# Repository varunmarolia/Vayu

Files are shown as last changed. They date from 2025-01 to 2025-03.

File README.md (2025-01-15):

# Vayu
Vayu is a smart ventilation system with heat recovery

# Problem
During winter time when the temperature is in single digit or below, the windows are kept shut and sealed so that radiators can work their magic.
The quality of indoor air gets very bad as the day goes by. The current ventilation system is basically a hole (ranging rom 100mm to 150mm in diameter) in the wall with some filter and vent with open/close mechanism.
This system does not provide enough air flow inside room specifically when the room is sealed. In order to make the indoor quality better the air needs to be forced/pumped inside the room.
Since the outside temperature is very low it needs to be heated and filtered before it can be pulled inside the room. 

# Focus of the project
- The aim of the project is to provide a ventilation system that can provide fresh room temperature air. We do this by recovering the heat from the air in the room itself.
- The system must be smart enough such that the "Heat recovery" should be performed automatically. i.e. if the outside temperature air is cold, turn on the heat recovery, if not just do normal ventilation.
- The design must be a quiet one, so we can sleep peacefully.
- Proper condensation management and defrosting functions.
- The system should have wireless capabilities in order to be an IoT device in the future.

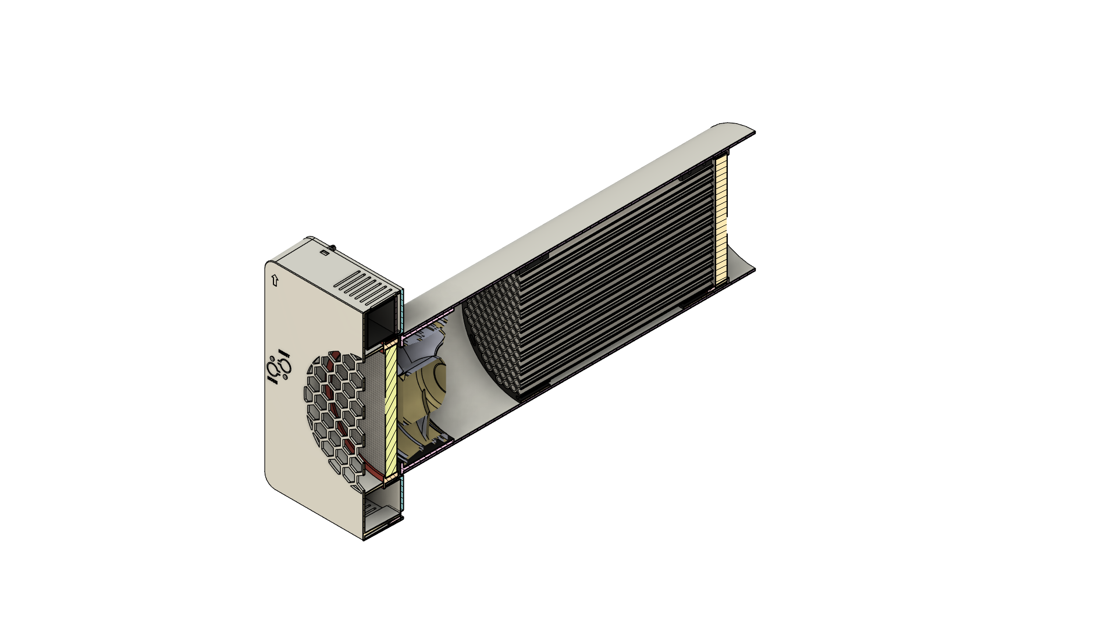
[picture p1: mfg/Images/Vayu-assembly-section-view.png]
Vayu full assembly Vayu-assembly-section-view-image

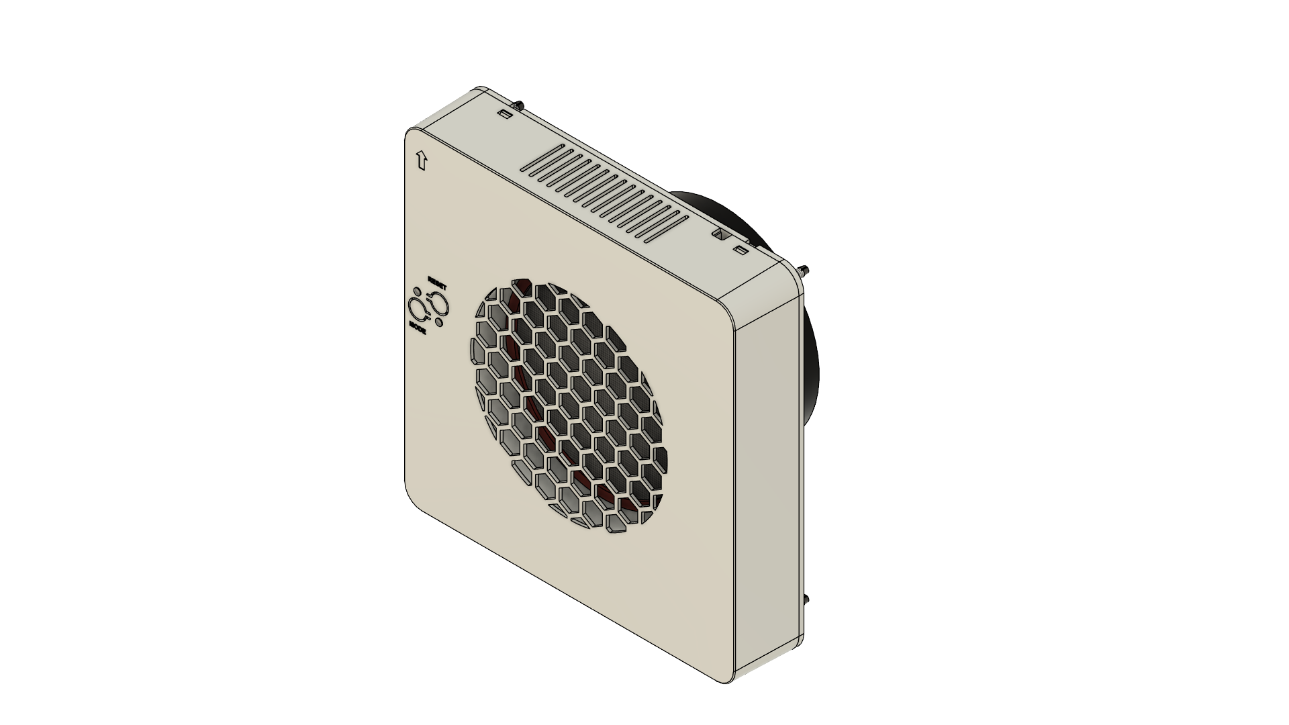
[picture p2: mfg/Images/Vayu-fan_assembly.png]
Vayu fan assembly Vayu-fan_assembly-image

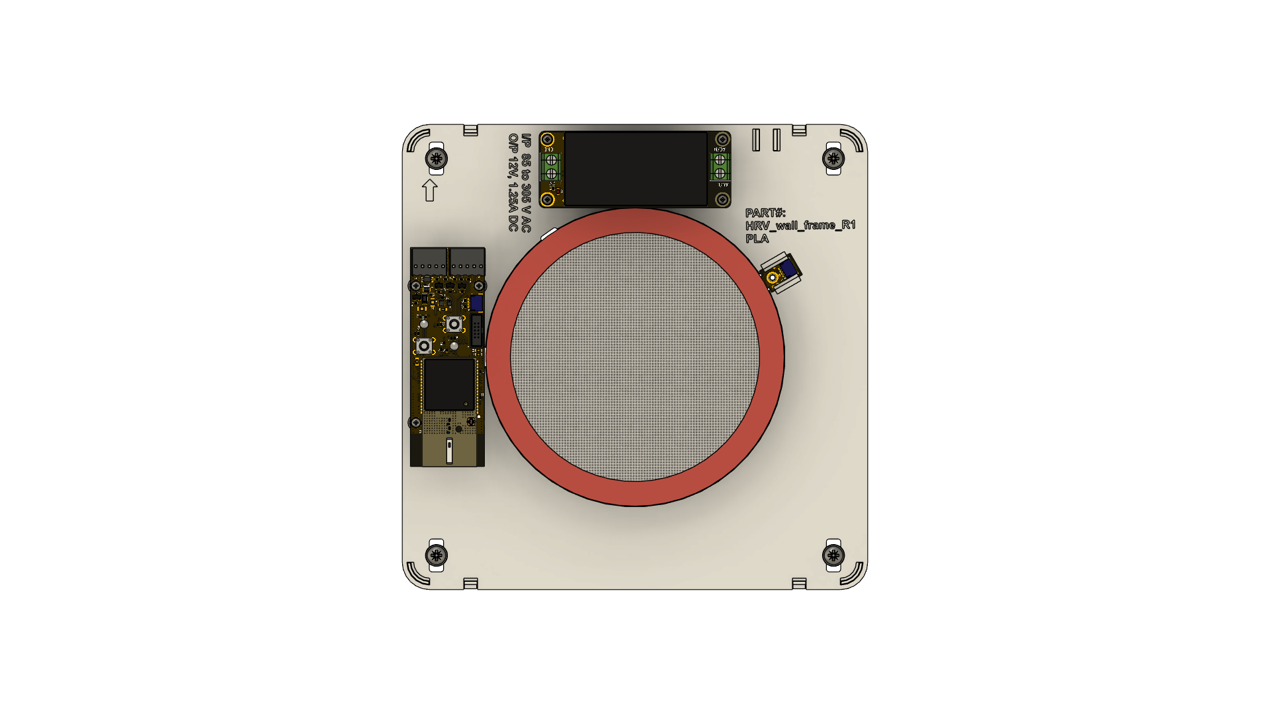
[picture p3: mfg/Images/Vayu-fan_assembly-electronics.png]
Vayu el assembly Vayu-el-image

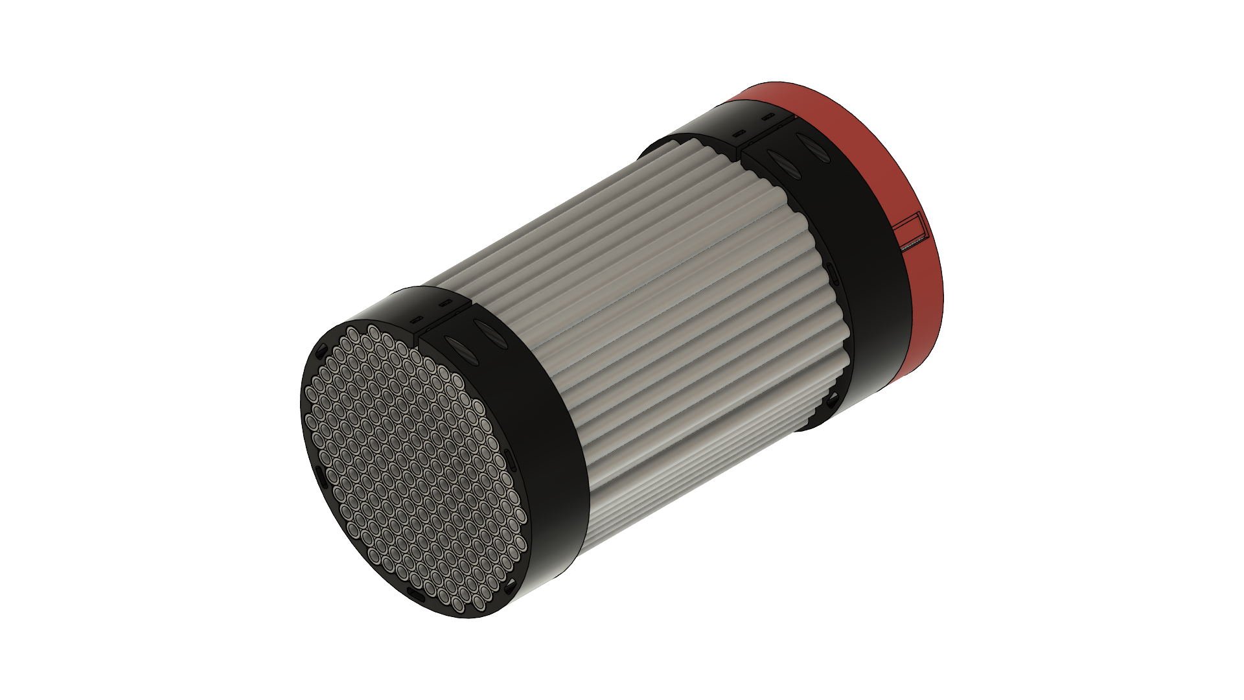
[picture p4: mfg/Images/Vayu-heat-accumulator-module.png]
Vayu heat accumulator Vayu-heat-accumulator-image


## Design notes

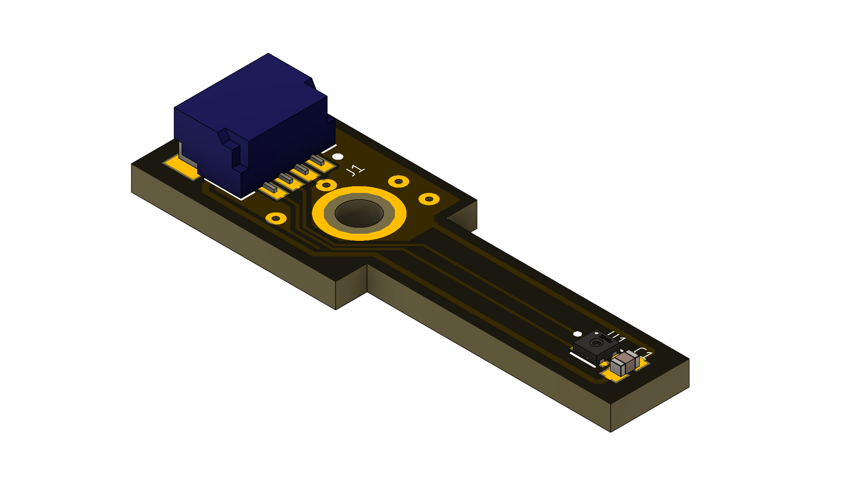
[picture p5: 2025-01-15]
mfg/Images/vayu_i2c-R1A-pcb-top-side.png

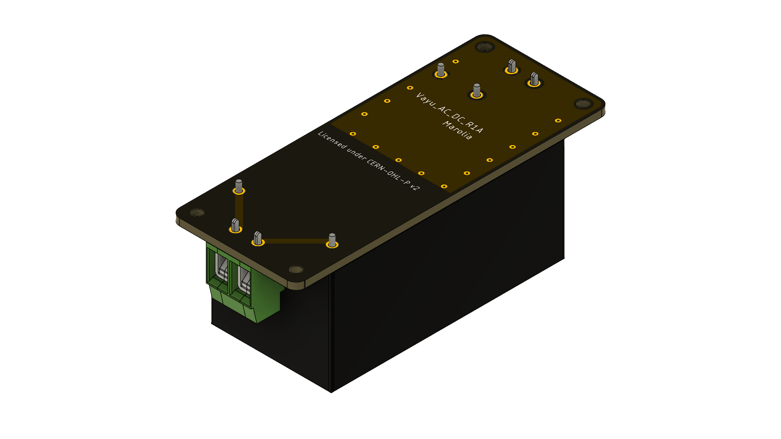
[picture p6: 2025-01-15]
mfg/Images/Vayu_AC_DC-R1A-pcb-bottom-side.png

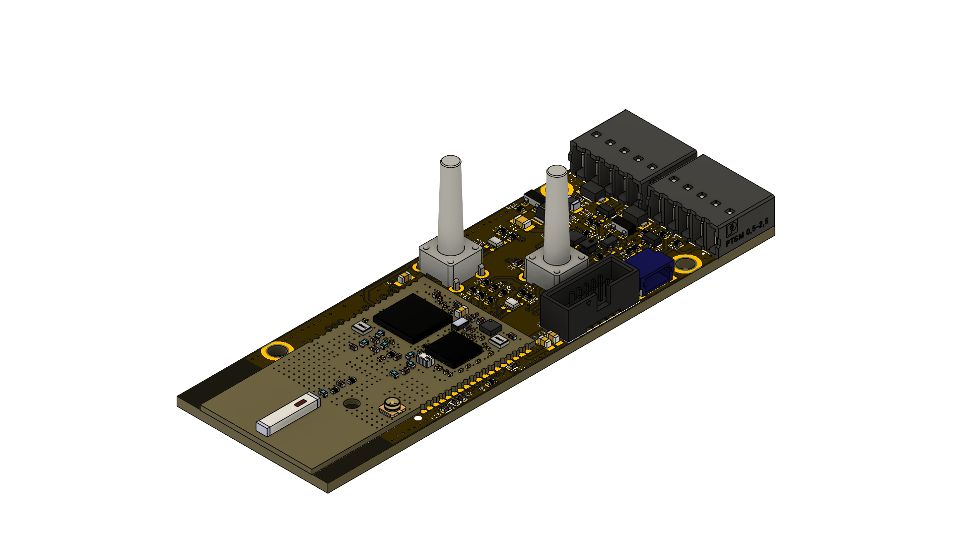
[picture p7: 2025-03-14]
mfg/Images/vayu-R1A-pcb_top_side.png

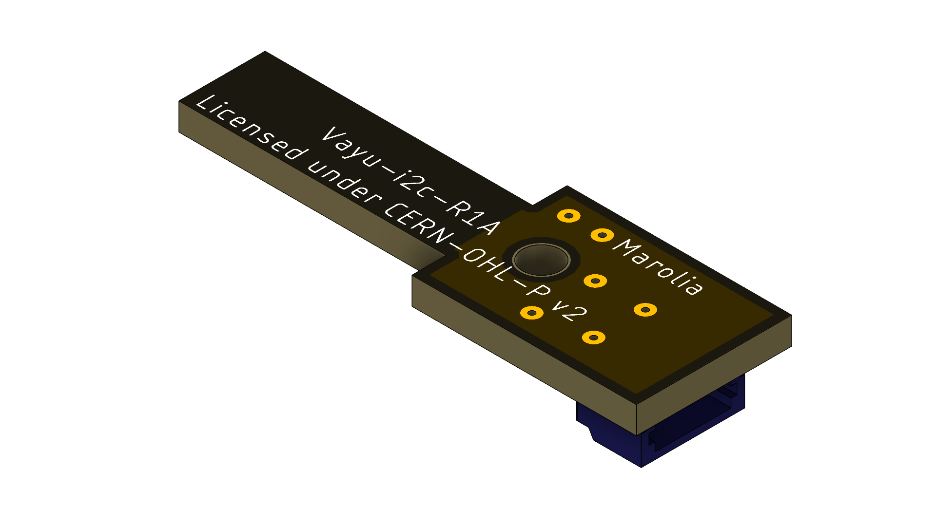
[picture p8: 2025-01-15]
mfg/Images/Vayu_i2c-R1A-pcb-bottom-side.png

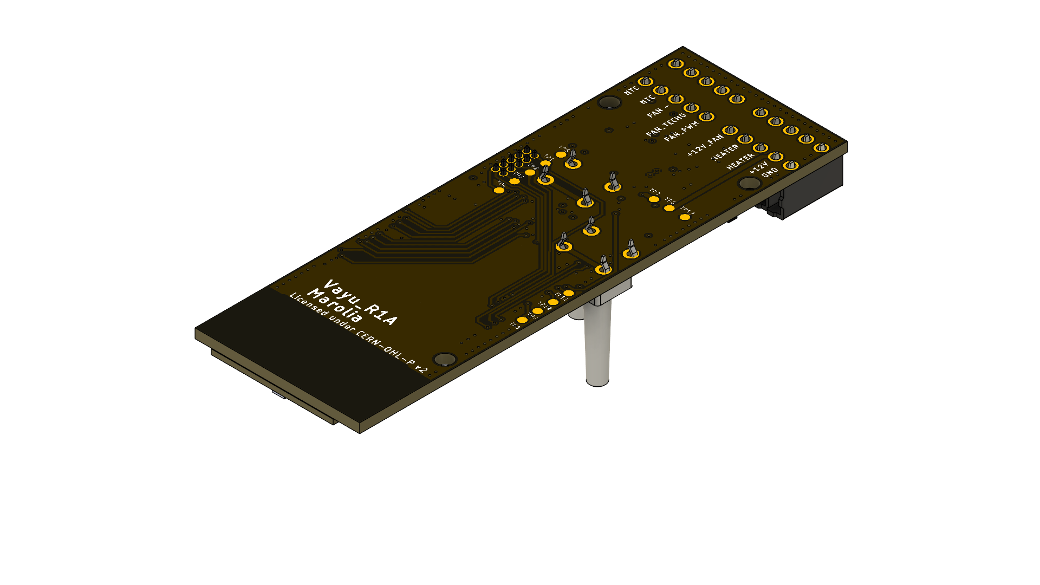
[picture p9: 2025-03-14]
mfg/Images/Vayu-R1A-pcb-bottom-side.png

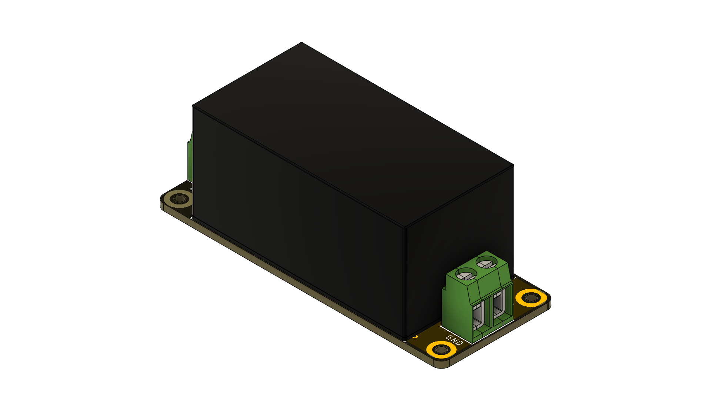
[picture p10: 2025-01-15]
mfg/Images/Vayu_AC_DC-R1A-pcb-top-side.png

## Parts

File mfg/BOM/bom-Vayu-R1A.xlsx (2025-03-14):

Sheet: Information
Title: | BILL OF MATERIAL
Project: | Vayu
Document: | bom-Vayu-R1A
Revision: | A
Date: | Oct/01/2024
PCBA P/N: | PCBA-Vayu-R1A
Notes:
Tab "No Mount" contains items that is not to be mounted
The revision of the BOM is same as revision of the Schematic
There are three different catagories of components
Cat "A" means component does not have any alternate manufacturers available
Cat "B" must choose from the list of manufacutrers provided
Cat "C" Can choose any manufacutrer as long as specifications for the components are met
PCBA part number is made of "PCBA-<code_name>-<pcb rev><schematic rev>
Changes in rev A |  | Oct/01/2024
Component | Part Reference | Comment
- | - | -

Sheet: Vayu
Marolia - Compressed sheet - Project: Vayu, Doc: bom-Vayu-R1A, Rev: A, Date: Oct/01/2024
Value | Title | Package | Qty | References | Assy | Cat | Mfr | Mfr PN | Mfr2 | Mfr PN2 | Mfr3 | Mfr PN3
1M | RESISTOR, 1%, 1/16W, SMT, RoHS | R0402 | 1 | R2 | SMT | C | Yageo | RC0402FR-071ML | Samsung | RC1005F105CS
10K | RESISTOR, 1%, 1/16W, SMT, RoHS | R0402 | 7 | R5, R3, R15, R16, R17, R23, R26 | SMT | C | Yageo | RC0402FR-0710KL | Samsung | RC1005F103CS
220E | RESISTOR, 1%, 1/16W, SMT, RoHS | R0402 | 4 | R18, R19, R20, R21 | SMT | C | Yageo | RC0402FR-07220RL | Samsung | RC1005F221CS
200K | RESISTOR, 1%, 1/16W, SMT, RoHS | R0402 | 2 | R22, R10 | SMT | C | Yageo | RC0402FR-07200KL
47K | RESISTOR, 1%, 1/16W, SMT, RoHS | R0402 | 2 | R7, R24 | SMT | C | Yageo | RC0402FR-1347KL | Bourns Inc. | CR0402-FX-4702GLF
100K | RESISTOR, 1%, 1/16W, SMT, RoHS | R0402 | 9 | R1, R4, R6, R8, R11, R12, R13, R14, R25 | SMT | C | Yageo | RC0402FR-07100KL | Samsung | RC1005F104CS
NCP15WF104F03RC | Thermistor, NTC, 100k OHM @ 25C, 1%, B=4250, 100mW, 0402 (1.0 x 0.5 x 0.5 mm), SMT, RoHS | R0402 | 1 | R9 | SMT | B | Murata | NCP15WF104F03RC
10uF | CAPACITOR, X5R, 6.3V, 20%, SMT, RoHS | C0603 | 3 | C1, C3, C4 | SMT | C | Murata | GRM188R60J106ME47D | Samsung | CL10A106MQ8NNNC
1nF | CAPACITOR, C0G NP0, 50V, 1%, SMT, RoHS | C0402 | 4 | C2, C12, C13, C14 | SMT | C | Murata | GCM1555C1H102FA16D | Yageo | AC0402FRNPO9BN102
10uF- 16V | CAPACITOR, X5R, 25V, 20%, SMT, RoHS | C0805 | 2 | C5, C11 | SMT | C | Murata | GRM21BR61E106MA73L | Samsung | CL21A106KACLRNC
22uF- 6V | CAPACITOR, X5R, 6.3V, 20%, SMT, RoHS | C0603 | 1 | C6 | SMT | C | Murata | GRM188R60J226MEA0D | Samsung | CL10A226MP8NUNE
0.1uF | CAPACITOR, X7R, 16V, 10%, SMT, RoHS | CAPC1005X55N | 4 | C7, C8, C9, C10 | SMT | C | Murata | GRM155R71E104KE14J | Samsung | CL05B104KO5NNNC
SMF12CA | Diode, Reverse standoff 12Volt- Breakdown 13.3V- 19.9V Clamp 10.1A Ipp Tvs Diode Surface Mount SOD-123F | SOD-123F-BI | 2 | D1, D3 | SMT | B | Littelfuse Inc. | SMF12CA | Shenzhen Slkormicro Semicon Co., Ltd. | SMF12CA
B240S1F-7 | Diode, MBR1020VL Surface Mount Schottky Power rectifier, >1.5Amp, DC reverse Max 16V | SOD-123F | 1 | D2 | SMT | B | Diodes Incorporated | B240S1F-7 | Diodes Incorporated | MBR230S1F-7
BLM21PG600SH1D | Ferrite bead, 60 Ohms @ 100 MHz 1 Power Line Ferrite Bead 0805 (2012 Metric) 3.5A 20mOhm | BEADC2012X105N | 1 | FB1 | SMT | B | Murata | BLM21PG600SH1D | Bourns Inc. | MH2029-600Y
CON-1770911 | Connector, 5 Position Wire to Board Terminal Block Horizontal with Board 0.098 (2.50mm) Through Hole | PHOENIX_1770911 | 2 | J1, J2 | TH | A | Phoenix Contact | 1770911
3220-10-0100-00 | Connector, Header Through Hole 10 position 0.050 (1.27mm) | PIN2X5_1.27MM | 1 | J3 | SMT | A | CNC Tech | 3220-10-0100-00
SM04B-SRSS-TB(LF)(SN) | Connector, Header Surface Mount, Right Angle 4 position 0.039" (1.00mm) | JST_SM04B-SRSS-TB(LF)(SN) | 1 | J4 | SMT | A | JST Sales America Inc. | SM04B-SRSS-TB
2.2uH- 1.84A | indcutor, 2.2 uH Shielded Drum Core- Wirewound Inductor 1.85 A 137mOhm Max 0806 (2016 Metric) | IND_VLS201612HBX-2R2M-1 | 1 | L1 | SMT | B | TDK Corporation | VLS201612HBX-2R2M-1 | Taiyo Yuden | MEKK2016H2R2M
IRLML6402TRPBF | MOSFET, P-Channel 20V 3.7A (Ta) 1.3W (Ta) Surface Mount SOT-23 | SOT23-3 | 2 | Q2,Q4 | SMT | C | Infineon | IRLML2244TRPBF | Taiwan Semiconductor Corporation | TSM650P02CX RFG
BSS138PW | MOSFET, N-Channel 60 V, 320 mA N-channel Trench MOSFET | SC-70 | 1 | Q1 | SMT | B | Nexperia USA Inc. | BSS138PW,115
DMN2056U-7 | N-Channel 20 V 4A (Ta) 940mW Surface Mount SOT-23-3 | SOT23-3 | 1 | Q3 | SMT | B | Diodes Incorporated | DMN2056U-7
MMBT4401WT1G | Bipolar (BJT) Transistor NPN 40 V 600 mA 250MHz 150 mW Surface Mount SC-70-3 (SOT323) | SC-70 | 1 | Q5 | SMT | B | Onsemi | MMBT4401WT1G
TL1105LF160Q | SWITCH, TACTILE SPST-NO 0.05A 12V 6x6mm. Actuator height from PCB 17mm | TACT_TH_6X6X17MM | 2 | SW1, SW2 | SMT | C | E-Switch | TL1105LF160Q
efr32-cc1200-rf | RF Module, Akshavani1 2.4GHz- 868/915 MHz radio module | AKASHVANI1 | 1 | U1 | SMT | A | Self | Akashvani1
TPS62172DSGT | Voltage regulator, TPS6217x 3-V to 17-V- 0.5-A Step-Down Converter swith DCS-Control | SON50P200X200X80-9N | 1 | U2 | SMT | A | Texas Instruments | TPS62172DSGT
APTB1615YSGC-F01 | LED, Bi-color, 568nm green/627nm red, 2.2V, 20mA, 1.6 x 1.5 mm, 0.7mm H, 4 pin, SMT, RoHS | LED-0606 | 2 | V1, V2 | SMT | B | Kingbright | APTB1615YSGC-F01

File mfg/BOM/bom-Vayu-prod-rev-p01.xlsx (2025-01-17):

Marolia - Top Level BOM for Vayu-R1A, Date: 2024-12-12, Rev: P01
Value | Title | Qty | Mfr | Mfr PN | Note
LFB075CTP | Light Pipe, 3mm dia, 19mm length, Single Clear, Diffused Rigid Panel Mount, Press Fit, Front | 2 | VCC | LFB050CTP | Front face center LED light pipe
1052620001 | Antenna, 866MHz, 915MHz Flat Patch, 0.4dBi, 1.4dBi U.FL (UMCC), IPEX MHF1 Adhesive | 1 | Molex | 1052620001 | Optinal Sub-GHz antenna
product-label | Fasson Transfer PET 75 / S8015 Matt silver heavy duty label 40mm x 25 mm | 1 | Fasson | PET75/S8015 | Silver label applied on back of the bottom plastic case
Vayu-front_shell | Mec, Front shell | 1 | 3d print | Vayu-front_shell
Vayu-wall_mounting_frame | Mec, Vayu wall mounting frame | 1 | 3d print | Vayu_wall_frame
Vayu-fan-shroude | Mec, Vayu fan shroude | 1 | 3d print | Vayu_fan_shroude
Vayu-filter_cap_front | Mec, Vayu filter cap front | 1 | 3d print | Vayu_filter_cap_front
heat_accumulator_filter_cap_back | Mec, heat-accumulator filter cap back | 1 | 3d print | Vayu_filter_cap_back
heat_accumulator_shroud | Mec, heat-accumulator shroud | 2 | 3d print | Vayu_heat_accumulator_shroude
Vayu-filter | Filter pad, 96 mm diameter | 2 | Flexit | friskluftsventil 100FF | Custom cut to 96mm diameter
PVC-pipe | Pipe, 100m diameter. 300mm length | 1 | Flexit | Flexit RG100 | Custom cut to wall length
M4 screw fan | screw,M4 x 16mm, self tapping plastic screw | 2 | Amazon
Anchor | Super plug, NY, 5mm hole, 25mm length, EXPANDET | 4 | Amazon
M4 wall screw | screw, M4 x 16mm length | 4 | Amazon
M2 screw | screw, M2.0, 5mm Length, Pan head, Philips OR Rouded head Torx Thread-forming screw for plastic | 8 | Amazon
M2 Nut | Nut, M2, Hex nut, 1.5mm thick, 3.8mm length | 4 | Amazon
SanAce_9RF_92x38_RBD | Fan Tubeaxial 12VDC Round - 92mm Dia Ball 42.4 CFM (1.19m³/min) 4 Wire Leads | 1 | Sanyo Denki America Inc. | 9RF0912P1H001
Vayu-R1A-PCBA | PCBA, Vayu-R1A, Assembled | 1 | Self assembled | Vayu-R1A-PCBA
Vayu_i2c-PCBA | PCBA, Vayu-i2c-R1A, Assembled | 1 | Self assembled | Vayu-i2c_R1A-PCBA
Vayu_AC_DC-PCBA | PCBA, Vayu_AC_DC-R1A, Assembled | 1 | Self assembled | Vayu_AC_DC-R1A-PCBA
Aluminium tubes | Tube, Aluminim, ID4mm, OD6mm, 166mm length | 211 | Kaiserthal | N/A | Bought from Hornbach and custom cut to 166mm
JST cable connector | 4 Position Cable Assembly Rectangular Socket to Socket, Reversed 0.667' (203.20mm, 8.00") | 1 | JST Sales America Inc. | A04SR04SR30K203A
AC-plug | plug, 2 pin AC cord, EU type, 2.5 meter | 1 | Amazon
magnet | magnet, Neodeam, 20mm x 10mm x 2mm | 1 | Amazon
Aluminium tape | tape, 50mm width, 250mm length, Metallic searing tape for high and low temperature channels, waterproof | 1 | Tesa | Tesa-60672
NTC-100K-probe | probe, NTC temperature probe, 100K, B3950 Thermistor, OD3mm Cartridge sensor | 1 | Amazon |  | Used in 3d printer extruder hot ends
Polymide-film-heater | Heater, Polymide film, 12Volt, 10watts, 30mm x 90mm | 1 | Amazon
Revision History
Rev | Date | Changes
P01 | 2024-12-12 | Initial release

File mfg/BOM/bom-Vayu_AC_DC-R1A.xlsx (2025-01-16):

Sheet: Information
Title: | BILL OF MATERIAL
Project: | Vayu_AC_DC
Document: | bom-Vayu_AC_DC-R1A
Revision: | A
Date: | DEC/01/2024
PCBA P/N: | PCBA-Vayu-R1A
Notes:
Tab "No Mount" contains items that is not to be mounted
The revision of the BOM is same as revision of the Schematic
There are three different catagories of components
Cat "A" means component does not have any alternate manufacturers available
Cat "B" must choose from the list of manufacutrers provided
Cat "C" Can choose any manufacutrer as long as specifications for the components are met
PCBA part number is made of "PCBA-<code_name>-<pcb rev><schematic rev>
Changes in rev A |  | Dec/01/2024
Component | Part Reference | Comment
- | - | -

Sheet: bom-Vayu_AC_DC-R1A
Marolia - Compressed sheet - Project: Vayu_AC_DC, Doc: bom-Vayu_AC_DC-R1A, Rev: A, Date: DEC/01/2024
Value | Description | Package | Qty | Reference | Assy | Cat | Mfr | Mfr PN | Mfr2 | Mfr PN2 | Mfr3 | Mfr PN3
CON-691137710002 | WR-TBL Serie 1377 - 5.00 mm Horiz Entry w. Pressure Clamp Glow Wire | TH-5MM | 2 | J1, J2 | TH | C | Würth Elektronik | 691137710002 | Same Sky (Formerly CUI Devices) | TB003-500-P02BE | Adam Tech | EBBA-02-C-SS-BU
IRM-15-12 | Meanwell Enclosed AC DC Converters 1 Output 12V 1.25A 85 ~ 305 VAC- 120 ~ 430 VDC Input | IRM-15 Series | IRM-15-12 | 15 watts | 12 volts | CONV_IRM-15-12 | 1 | PS1 | TH | A | Meanwell | IRM-15-12
680R | RESISTOR, 1%, 1/16W | R0402 | 1 | R1 | SMT | C | Yageo | RC0402FR-07680RL | Bourns Ic. | CR0402-FX-6800GLF
LED_RED | LED, Red 624nm LED Indication - Discrete 2V 0603 (1608 Metric) | CHIP-LED0603 | 1 | V1 | SMT | C | Harvatek Corporation | B1911USD-20D000114U1930 | Rohm Semiconductor | SML-D12U1WT86

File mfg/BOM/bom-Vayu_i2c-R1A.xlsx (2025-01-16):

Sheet: Information
Title: | BILL OF MATERIAL
Project: | Vayu
Document: | bom-Vayu_i2c-R1A
Revision: | A
Date: | Oct/01/2024
PCBA P/N: | PCBA-Vayu_i2c-R1A
Notes:
Tab "No Mount" contains items that is not to be mounted
The revision of the BOM is same as revision of the Schematic
There are three different catagories of components
Cat "A" means component does not have any alternate manufacturers available
Cat "B" must choose from the list of manufacutrers provided
Cat "C" Can choose any manufacutrer as long as specifications for the components are met
PCBA part number is made of "PCBA-<code_name>-<pcb rev><schematic rev>
Changes in rev A |  | Oct/01/2024
Component | Part Reference | Comment
- | - | -

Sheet: bom-Vayu_i2c-R1A
Marolia - Compressed sheet - Project: Vayu, Doc: bom-Vayu_i2c-R1A, Rev: A, Date: Oct/01/2024
Value | Title | Package | Qty | Reference | Assy | Cat | Mfr | Mfr PN | Mfr2 | Mfr PN2 | Mfr3 | Mfr PN3
0.1uF | CAPACITOR, X7R, 16V, 10%, SMT, RoHS | C0402 | 1 | C1 | SMT | C | Murata | GRM155R71E104KE14J | Samsung | CL05B104KO5NNNC
SHT40-AD1F-R2 | IC, Humidity, Temperature 0 ~ 100% RH I2C ±1.8% RH 4 s Surface Mount | 4-WDFN Exposed Pad | 1 | U1 |  | A | Sensirion AG | SHT40-AD1F-R2
SM04B-SRSS-TB(LF)(SN) | Connector, Connector Header Surface Mount, Right Angle 4 position 0.039" (1.00mm) | JST_SM04B-SRSS-TB(LF)(SN) | 1 | J1 | SMT | A | JST Sales America Inc. | SM04B-SRSS-TB

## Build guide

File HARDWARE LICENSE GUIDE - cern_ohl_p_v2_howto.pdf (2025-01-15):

# Guide to the CERN-OHL-P v2

This document contains guidelines on how to apply the CERN-OHL-P v2 to a given hardware design, and on the use of hardware designs licensed under the CERN-OHL-P v2.

How to apply the CERN-OHL-P v2 to a hardware design Pre-requisite:

Authorship/ownership of the design must be clear and undisputed. Only the legal owner of the rights in the hardware design may decide under what conditions to make it available. If ownership is vested in more than one person/entity, there must be an agreement among the owners (or a chain of compatible licences from each of them) to release the hardware design as open hardware, and under the CERN-OHL-P v2 in particular.

The hardware design Source package

Pack all your hardware design Source files (e.g. for a Printed Circuit Board schematics, layout, documentation...) as well as the documents listed below in an archive file. This will ensure the licensee downloads everything in one go. It is best to archive the files using a format everybody can open. Schematics and layouts should be included in both source form and, should the design tool be proprietary, a format readable by everybody, such as pdf.

The following documents must be distributed together with the hardware design sources:

- Document containing the CERN-OHL-P v2
- This Guide
- A text file (plain ASCII file), where information can be added to but not removed from, noting that the design has been changed, and providing a date and information about the changes made by Licensee (see section 3.3.b of CERN-OHL-P v2) (e.g. CHANGES.TXT). A detailed list of changes would be helpful, as would a diff, but a description of the changes (e.g. “AC/DC power converter circuit removed as AC input no longer necessary”) is fine.

What to do with the hardware design Sources

Include in the hardware design Sources, for instance as a header, the following elements:
- a copyright notice reflecting actual ownership;
- a notice that the hardware design source is licensed under the CERN-OHL-P v2, possibly with a link to https://cern.ch/cern-ohl:

o “Licensed under CERN-OHL-P v2 or later”

o “Licensed under CERN-OHL-P v2”;

- a disclaimer of warranties;
- a source location, where others can find your design, if you wish to specify one;

The following is an example of header if CERN is the Licensor:

Copyright CERN 2020.

This source describes Open Hardware and is licensed under the CERN-OHL-P v2

You may redistribute and modify this documentation and make products using it under the terms of the CERN-OHL-P v2 (https:/cern.ch/cern-ohl). This documentation is distributed WITHOUT ANY EXPRESS OR IMPLIED WARRANTY, INCLUDING OF MERCHANTABILITY, SATISFACTORY QUALITY AND FITNESS FOR A PARTICULAR PURPOSE. Please see the CERN-OHL-P v2 for applicable conditions

Include in a part of the Source corresponding to a visible part of the Product (e.g. silkscreen or top copper for a Printed Circuit Board):

- the licence notice: “Licensed under CERN-OHL-P v2”

o Do not include the CERN logo or the copyright notice

- the source location if you wish it to appear on the Product, its packaging or documentation

How to deal with hardware designs licensed under the CERN-OHL-P v2
Generally speaking, you must always comply with any obligations applying to a particular design (detailed in a contract or accompanying licence). If you receive hardware designs licensed under the CERN-OHL-P v2, the obligations are to:
- Keep intact all the copyright and trademark notices that are on the hardware design Sources;
- Keep intact the references to the CERN-OHL-P v2;
- Keep intact the disclaimer of warranties.

If you modify hardware design that you received from someone else that is licensed under the CERN-OHL-P v2, you must

- Keep intact all the notices referred to above (although you may remove notices that are no longer relevant to your design (for example, if the design you are using contains a power supply and a processor board, and you are only using the processor board in your own design, you can remove the notices relating to the power supply, so long as you are sure they only relate to the power supply);
- Include notices that you have modified the hardware designs, giving a date and information about the modifications you have made (e.g. in a CHANGES.TXT file);
- Add the appropriate copyright notice to the modifications that were made;

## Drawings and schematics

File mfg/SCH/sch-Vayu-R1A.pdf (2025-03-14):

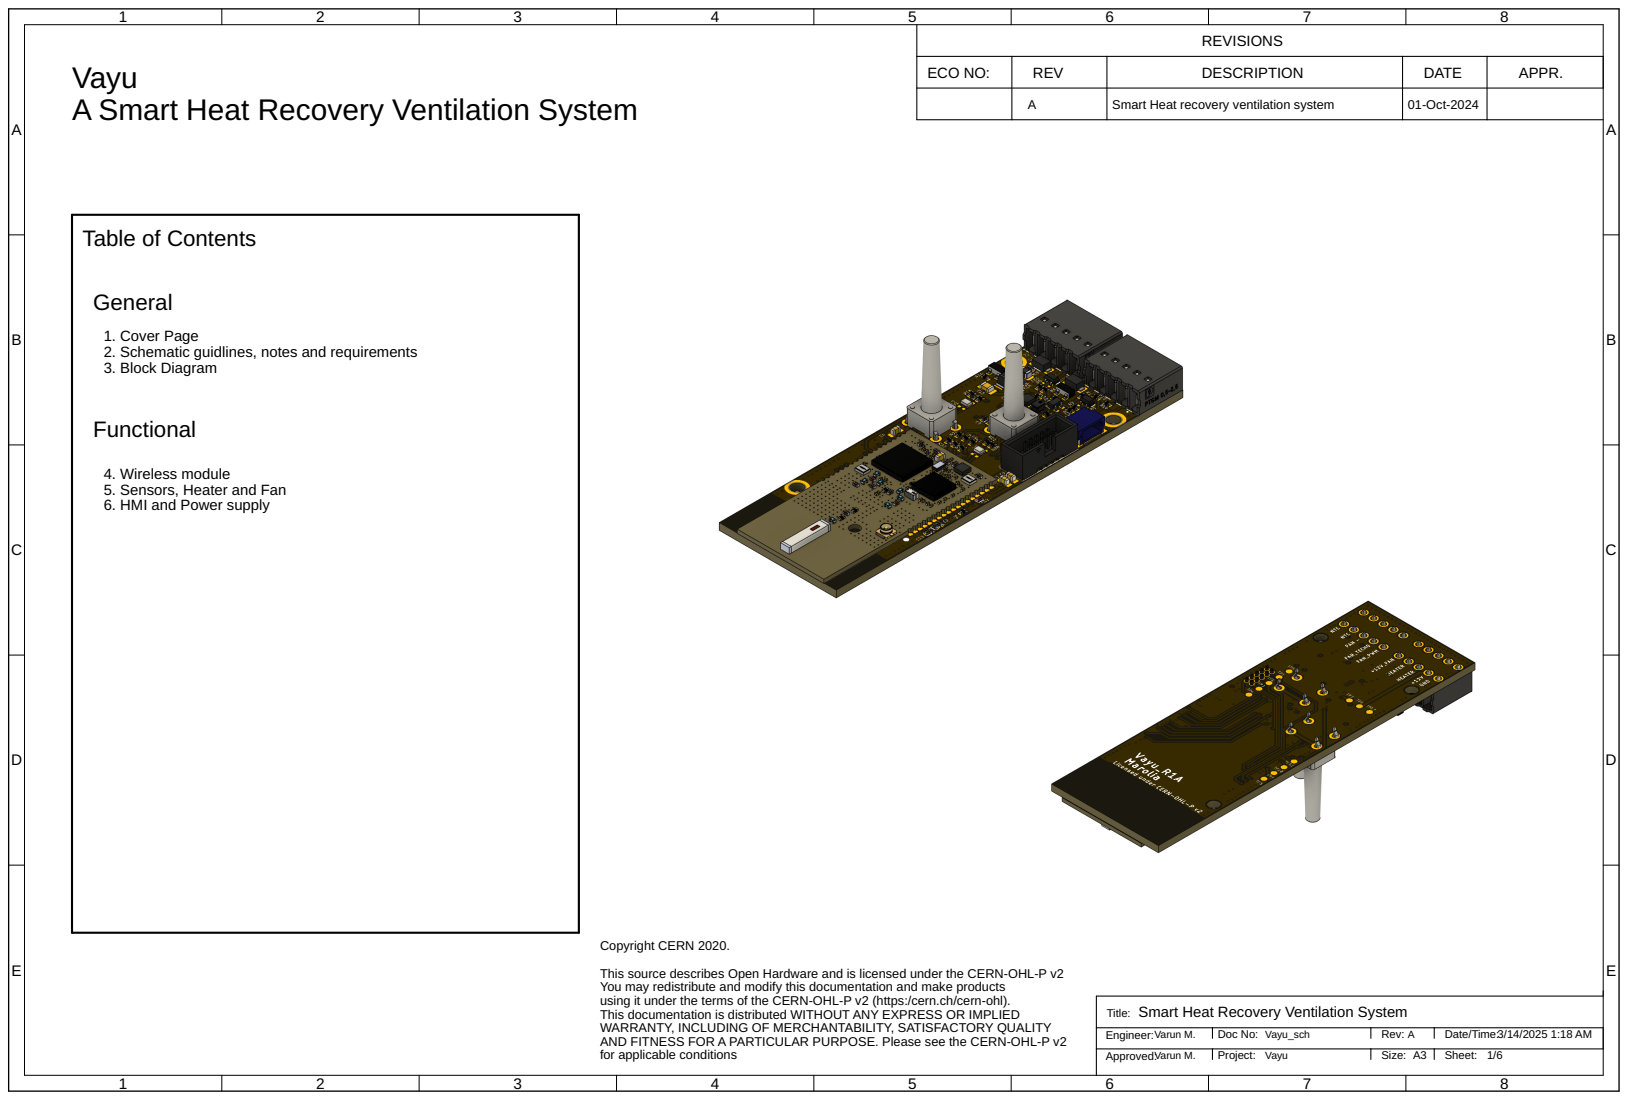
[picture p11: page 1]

REVISIONS

Vayu
A Smart Heat Recovery Ventilation System

ECO NO: | REV | DESCRIPTION | DATE | APPR.

A | Smart Heat recovery ventilation system | 01-Oct-2024

1. Cover Page
2. Schematic guidlines, notes and requirements
3. Block Diagram

4. Wireless module
5. Sensors, Heater and Fan
6. HMI and Power supply

Copyright CERN 2020. This source describes Open Hardware and is licensed under the CERN-OHL-P v2

You may redistribute and modify this documentation and make products
using it under the terms of the CERN-OHL-P v2 (https:/cern.ch/cern-ohl). This documentation is distributed WITHOUT ANY EXPRESS OR IMPLIED

Smart Heat Recovery Ventilation System

WARRANTY, INCLUDING OF MERCHANTABILITY, SATISFACTORY QUALITY
AND FITNESS FOR A PARTICULAR PURPOSE. Please see the CERN-OHL-P v2
for applicable conditions

Schematic guidelines, notes and requirements

# Schematic guidelines, notes and requirements

## Component guidelines

0 ohm resistors are 0402, 1A, unless otherwise noted. Capacitors are 0402, 10%, 50V unless otherwise noted. 0.047uF capacitors are 0402, 10%, 25V unless otherwise noted. 0.1uF, 0.22uF, 0.47uF and 1uF capacitors are 0402, 10%, 16V unless otherwise noted. 4.7uF, 10uF, and 22uF bulk capacitors are 0603, 6.3V/10V unless otherwise noted. Test point diameter is 1.2mm unless otherwise noted. Schematic guidelines

## General

IC pins that are internally pulled up or pulled down are indicated with the text PU or PD. All power nets normally starts with capital VDD* or VCC*. These nets should have planes by default. Graphic symbol description

Digital ground

Voltage connection

Test point (default size)

## Rules

Test points must be placed on the Secondary (bottom) side with a minimum 2.54mm spacing unless otherwise noted. Surface mount components on secondary side if any must be at least 4mm from thru hole pins. Not applicable for test

pins and debug headers (manually assembled when needed). Keep ground plane(s) away from the radio section of the wireless module. The 868/915 MHz radio on the wireless module uses external antenna that

must be encapulated inside the product case while avoiding proximity to any ground planes.

Sheet: Date/Time: Title: Engineer: | Doc No: | Rev: Approved: | Project: | Size: A3

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

A

B | B
C | C
D | D

E

A

E

3/14/2025 1:18 AM

2/6

Varun M. | Vayu_sch Vayu | A

Varun M.

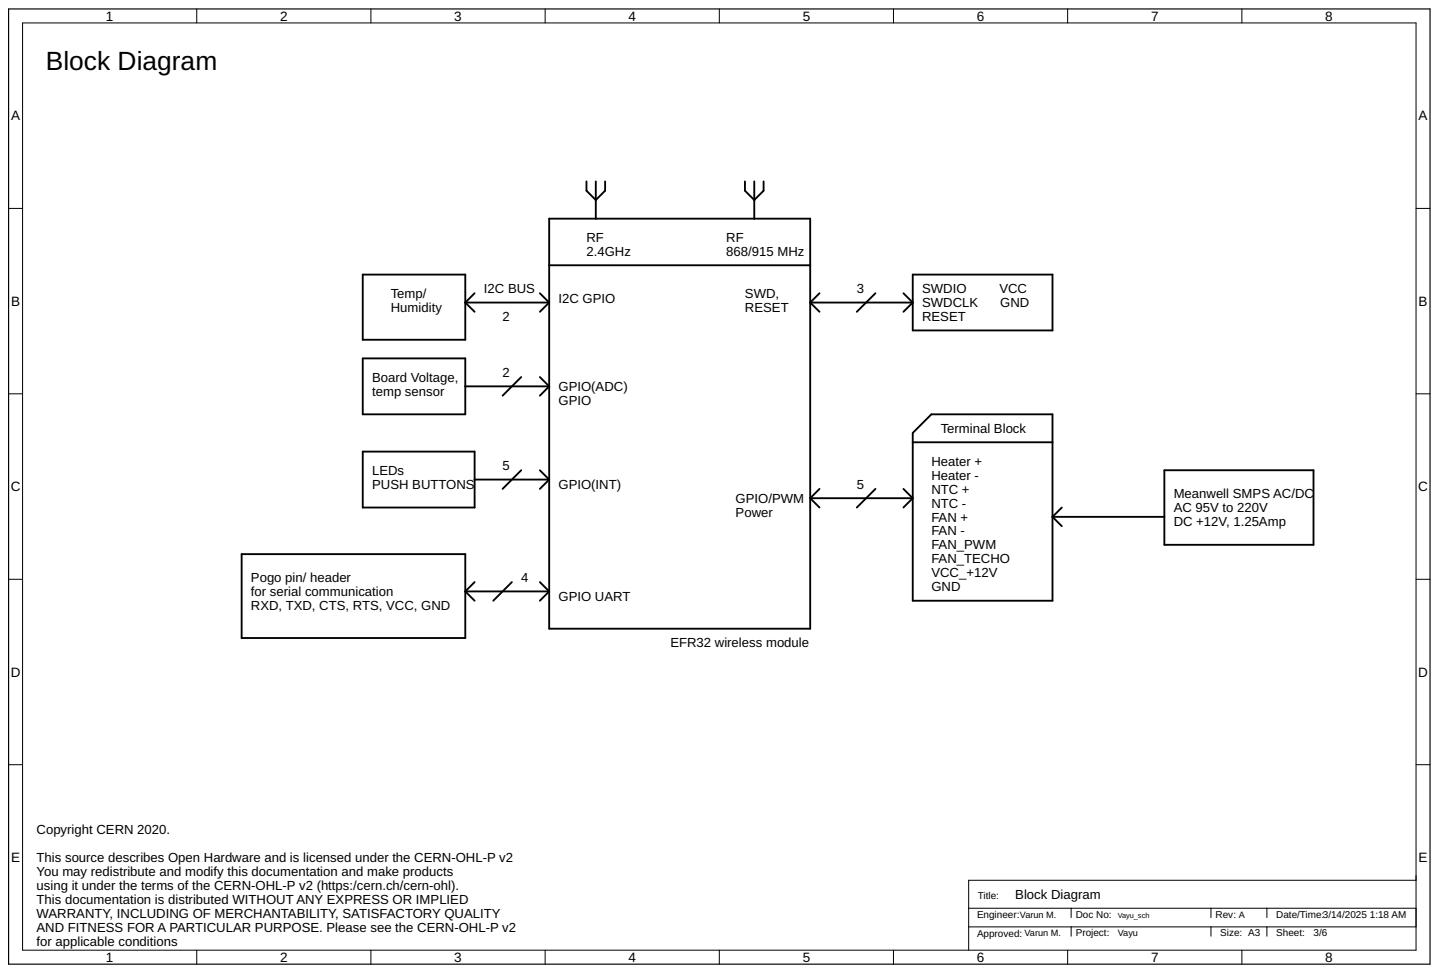
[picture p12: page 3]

Meanwell SMPS AC/DC
DC +12V, 1.25Amp

Pogo pin/ header
for serial communication
RXD, TXD, CTS, RTS, VCC, GND

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

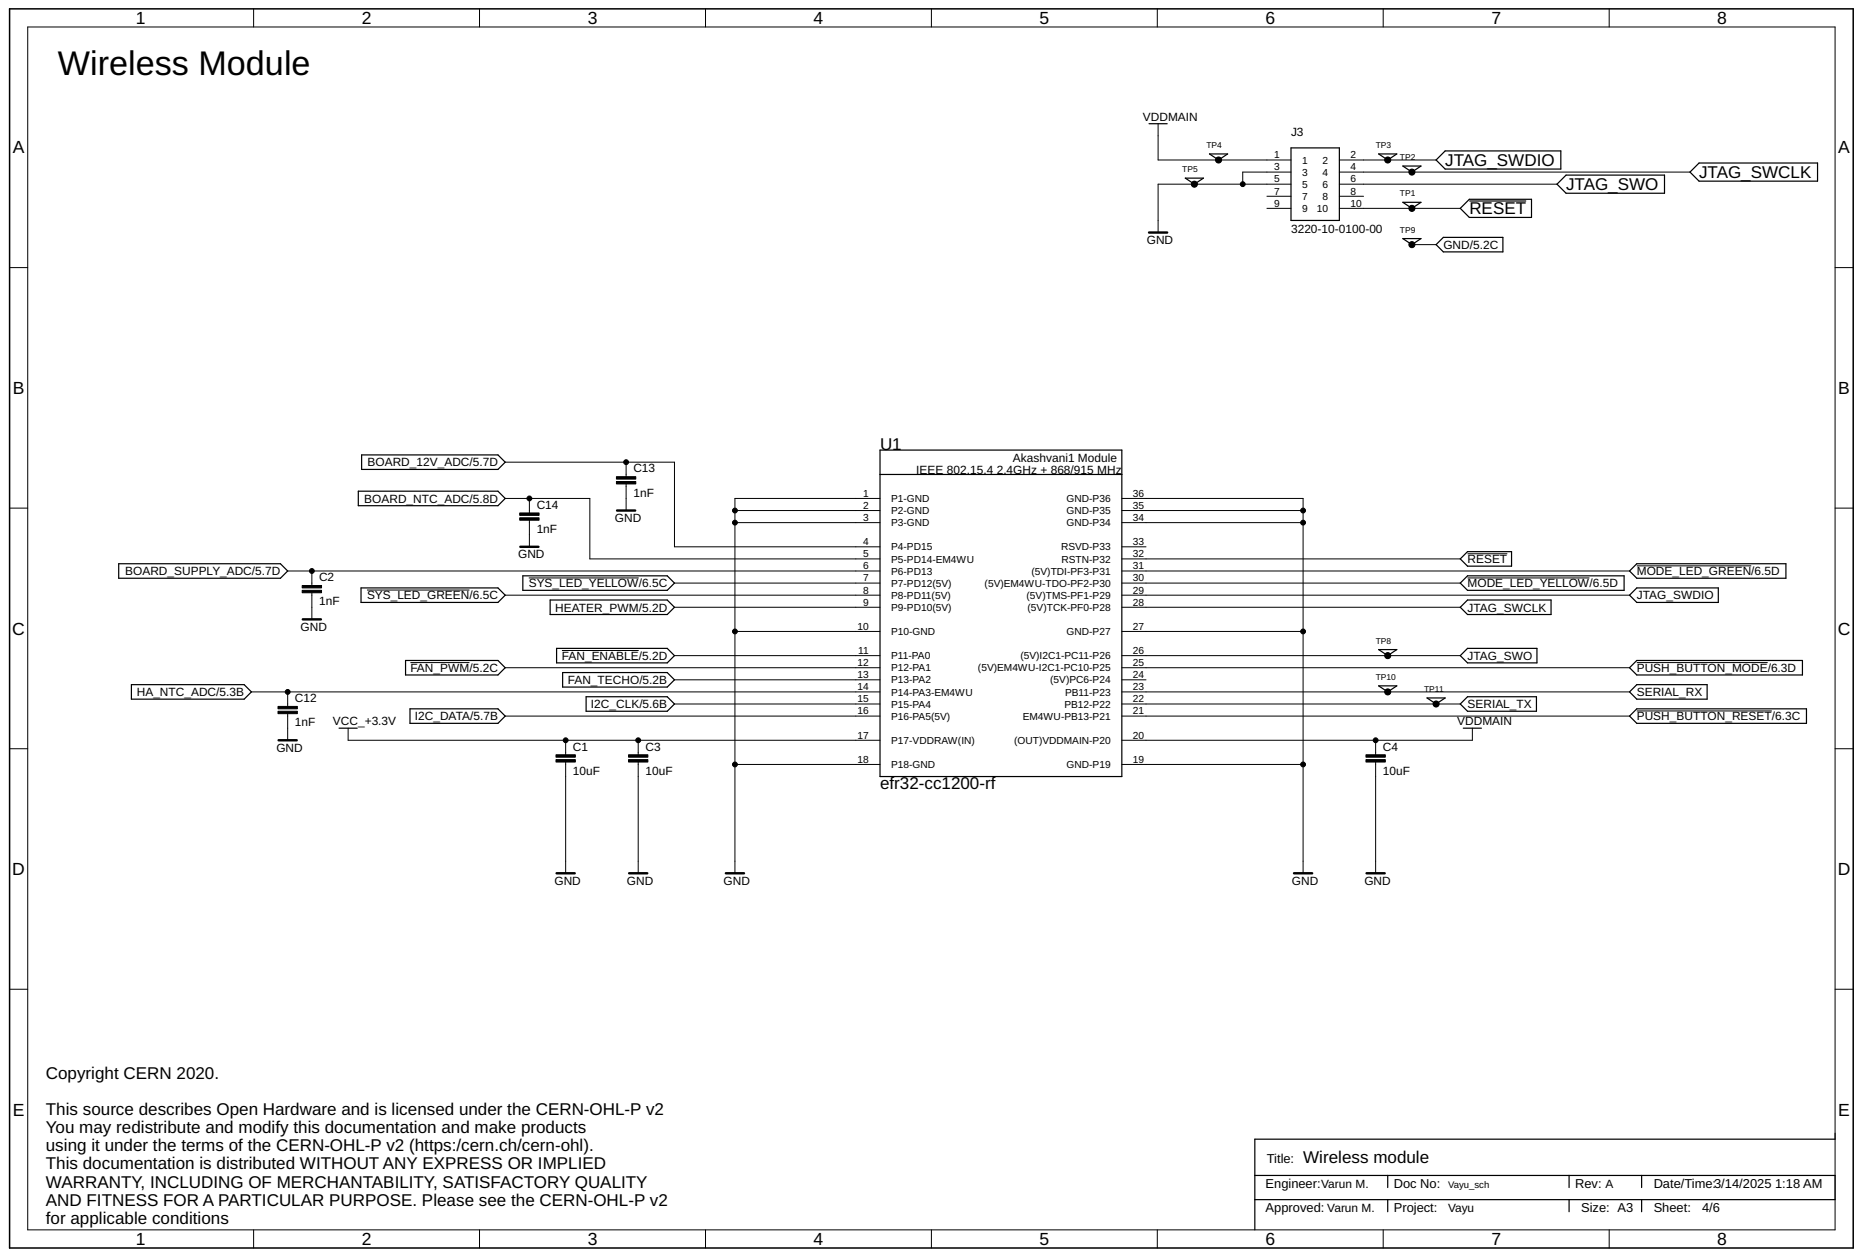
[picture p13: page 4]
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

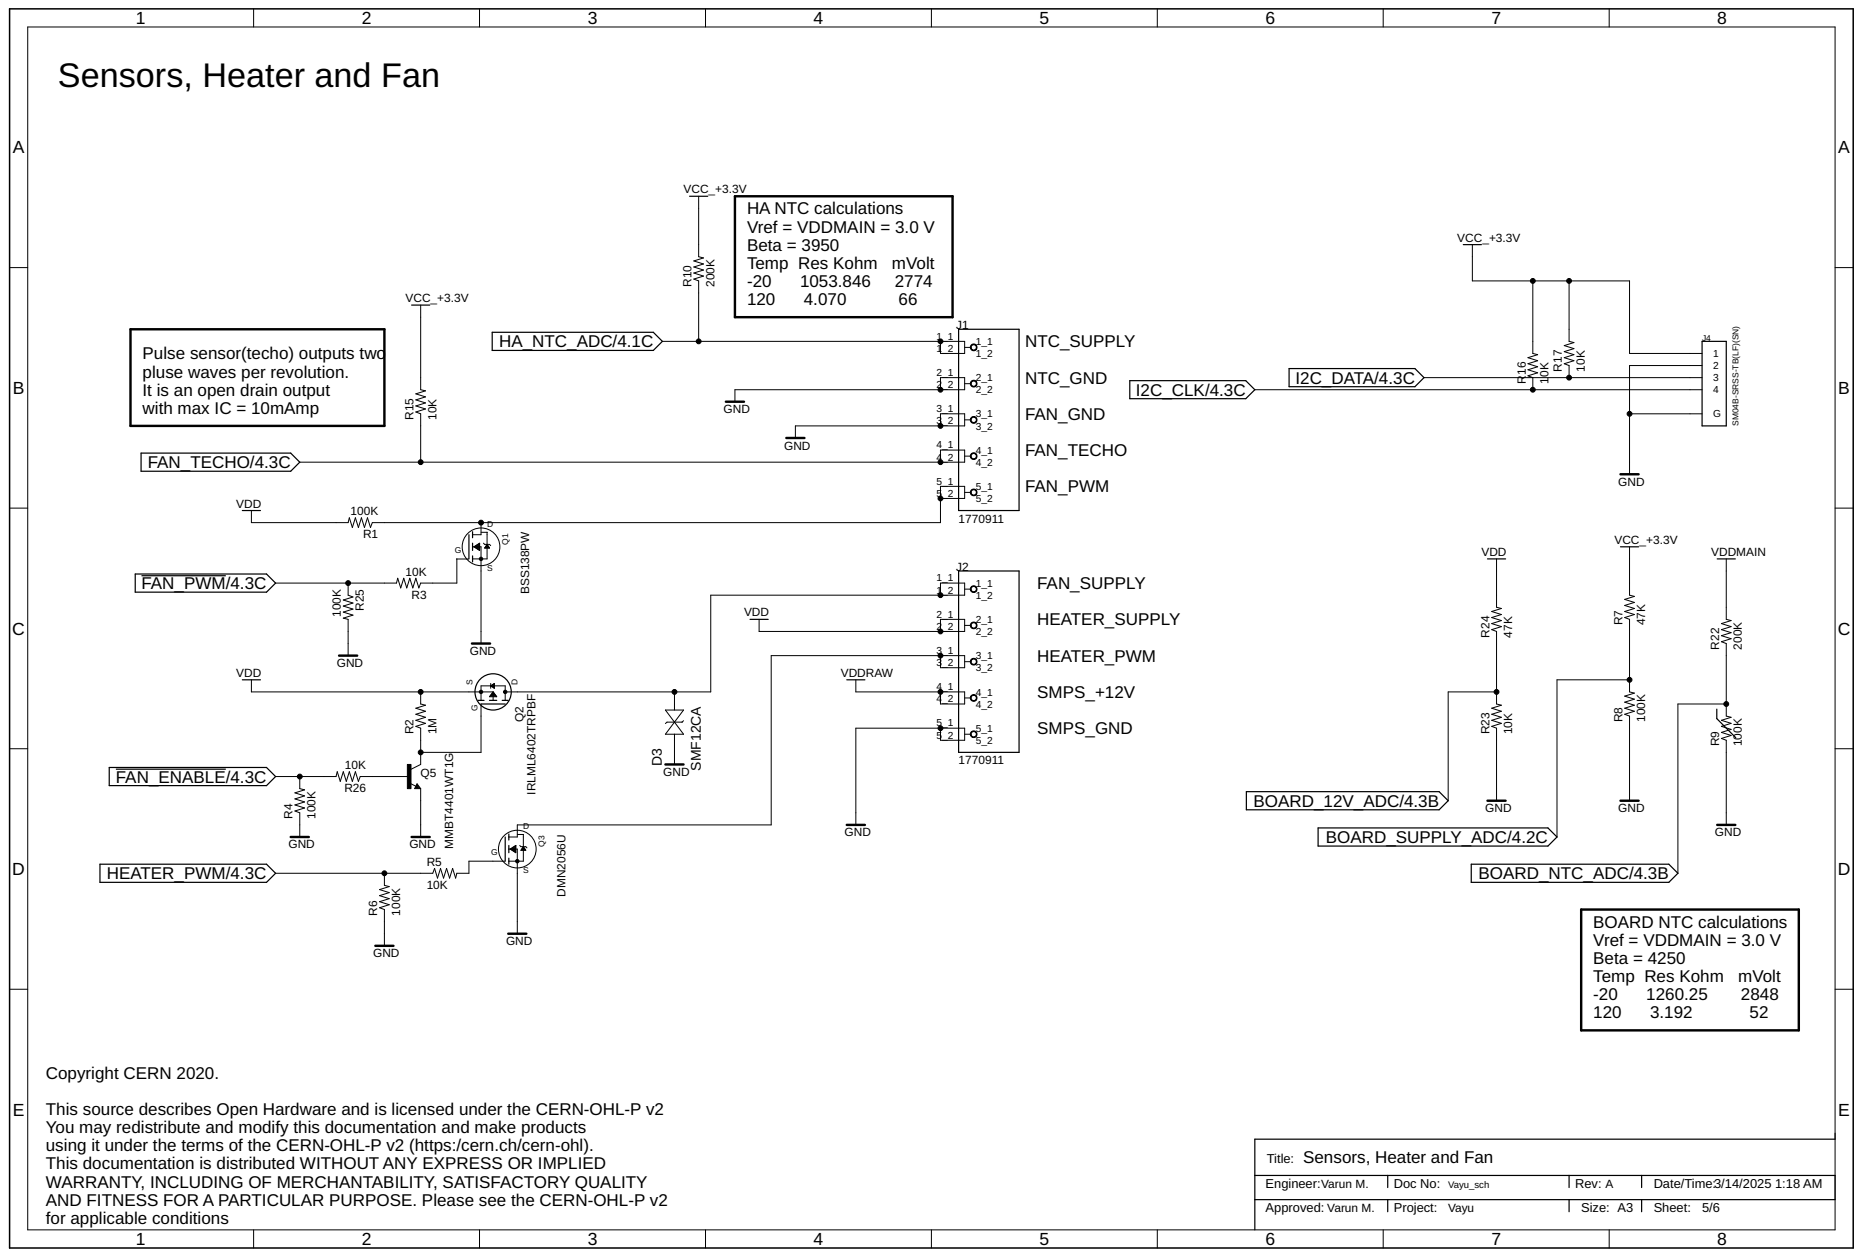
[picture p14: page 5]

Sensors, Heater and Fan

SM04B-SRSS-TB(LF)(SN)

Pulse sensor(techo) outputs two
pluse waves per revolution.
It is an open drain output
with max IC = 10mAmp

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

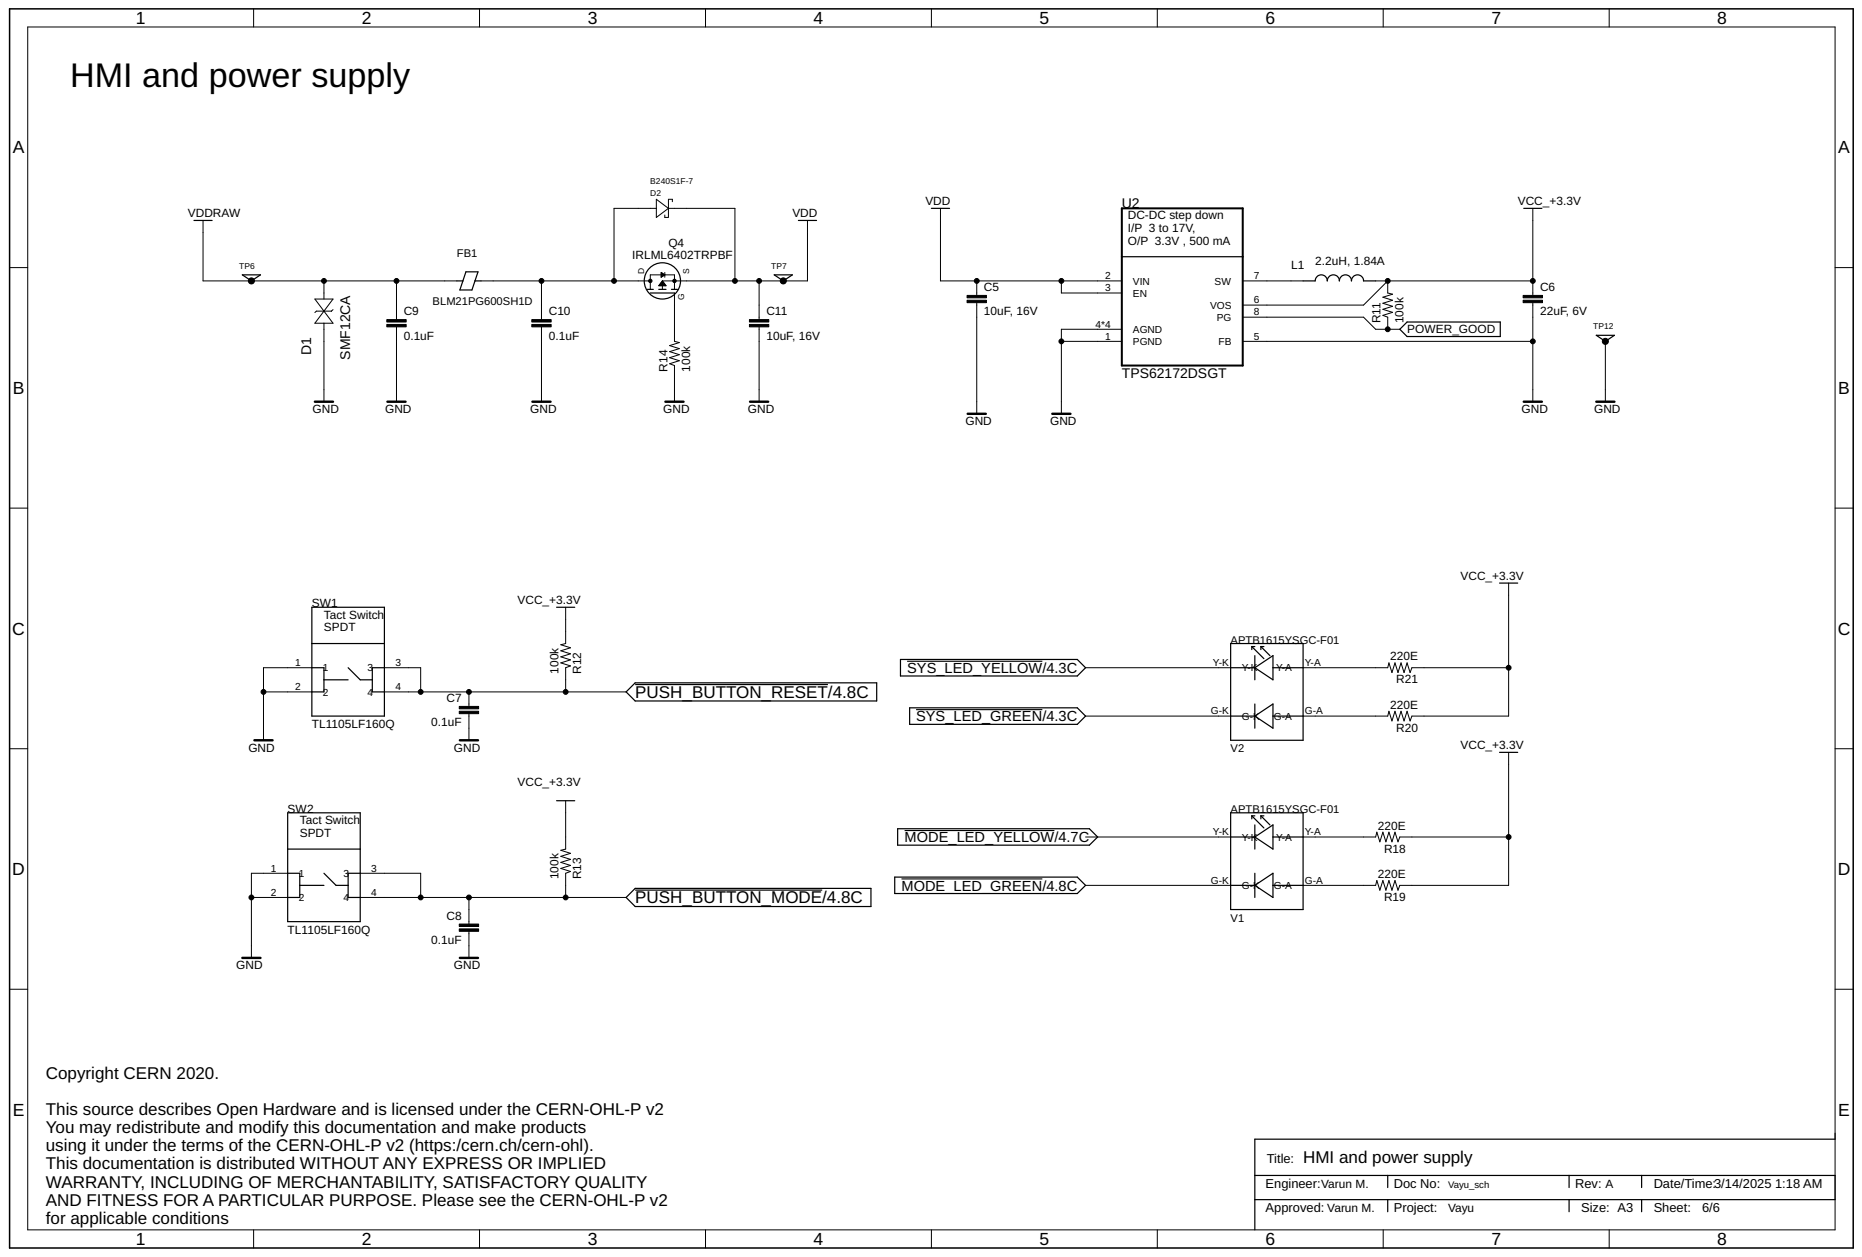
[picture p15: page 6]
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

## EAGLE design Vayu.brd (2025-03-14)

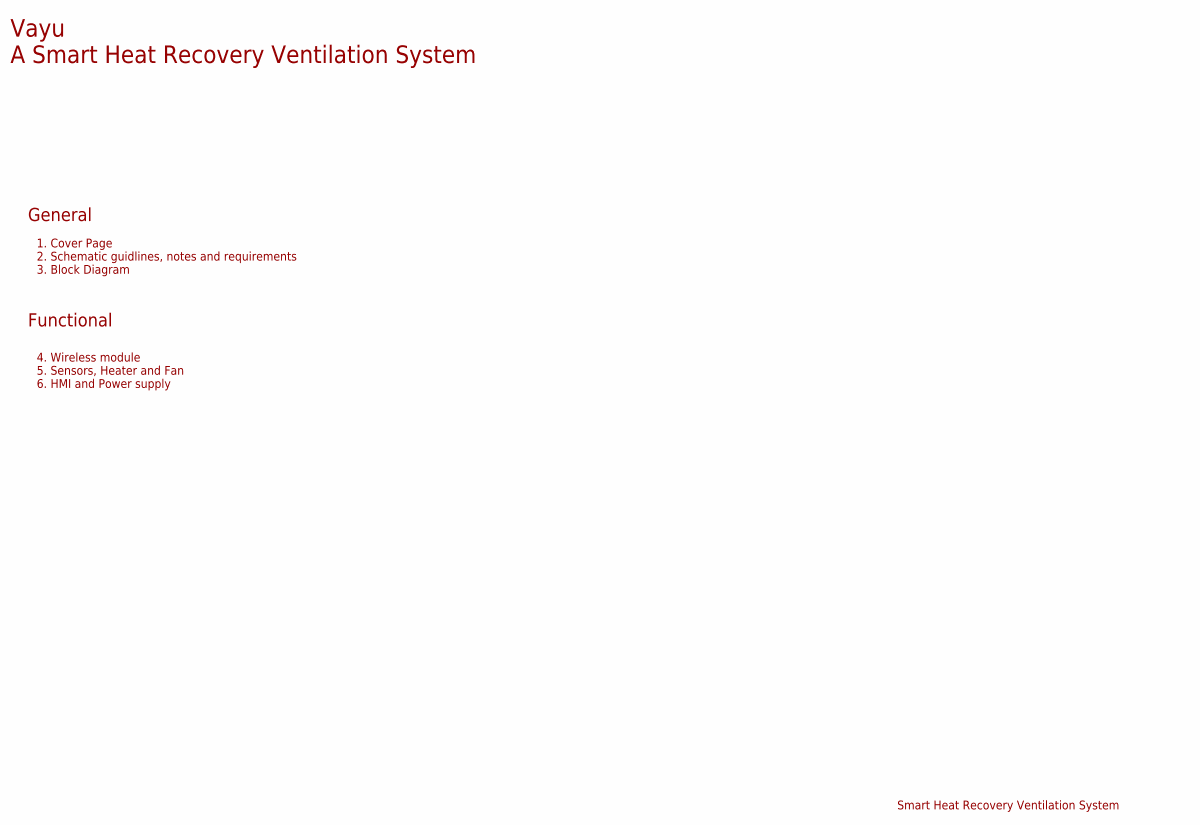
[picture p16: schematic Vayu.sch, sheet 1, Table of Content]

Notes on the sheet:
Smart Heat Recovery Ventilation System
General
1. Cover Page 2. Schematic guidlines, notes and requirements 3. Block Diagram
Functional
4. Wireless module 5. Sensors, Heater and Fan 6. HMI and Power supply
Vayu A Smart Heat Recovery Ventilation System

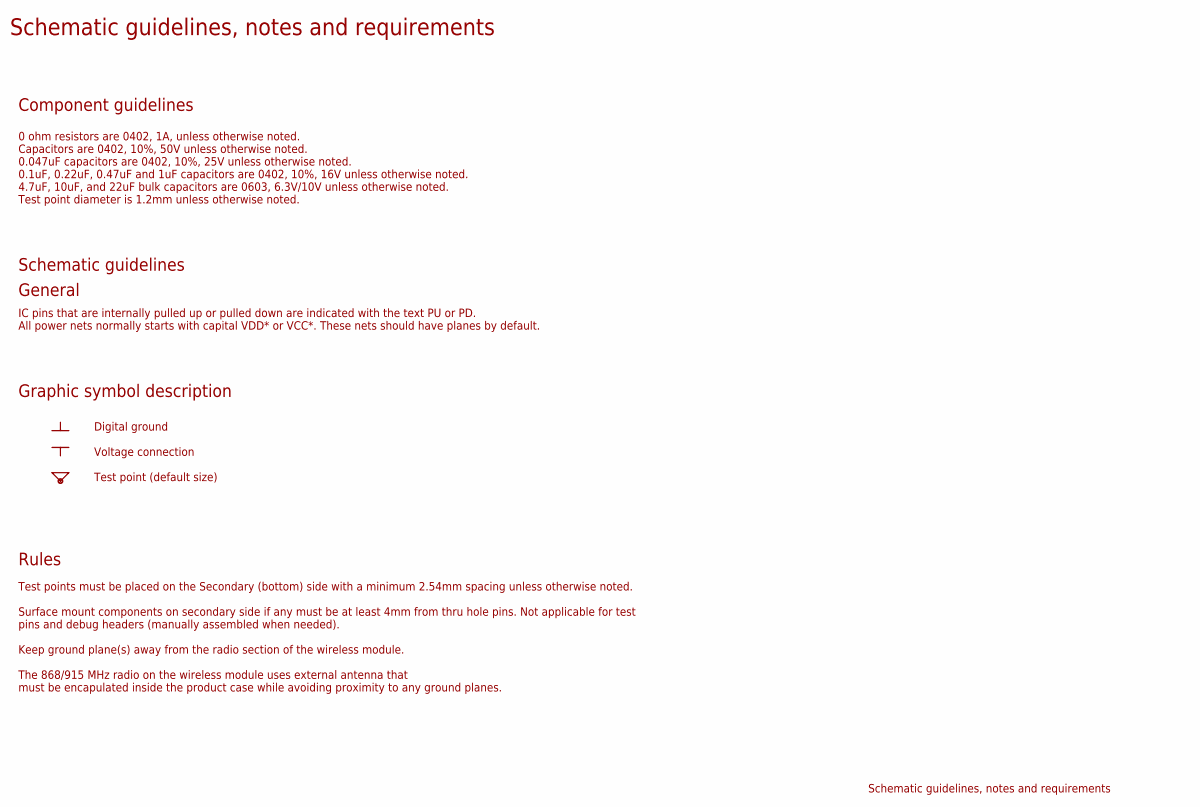
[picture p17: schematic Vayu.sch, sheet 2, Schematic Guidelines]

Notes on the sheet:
Schematic guidelines, notes and requirements
Component guidelines
0 ohm resistors are 0402, 1A, unless otherwise noted. Capacitors are 0402, 10%, 50V unless otherwise noted. 0.047uF capacitors are 0402, 10%, 25V unless otherwise noted. 0.1uF, 0.22uF, 0.47uF and 1uF capacitors are 0402, 10%, 16V unless otherwise noted. 4.7uF, 10uF, and 22uF bulk capacitors are 060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
Schematic guidelines
General
IC pins that are internally pulled up or pulled down are indicated with the text PU or PD. All power nets normally starts with capital VDD* or VCC*. These nets should have planes by default.
Graphic symbol description
Digital ground Voltage connection Test point (default size)
Rules
Test points must be placed on the Secondary (bottom) side with a minimum 2.54mm spacing unless otherwise noted. Surface mount components on secondary side if any must be at least 4mm from thru hole pins. Not applicable for test pins and debug headers (manually assembled when needed). Keep ground pl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

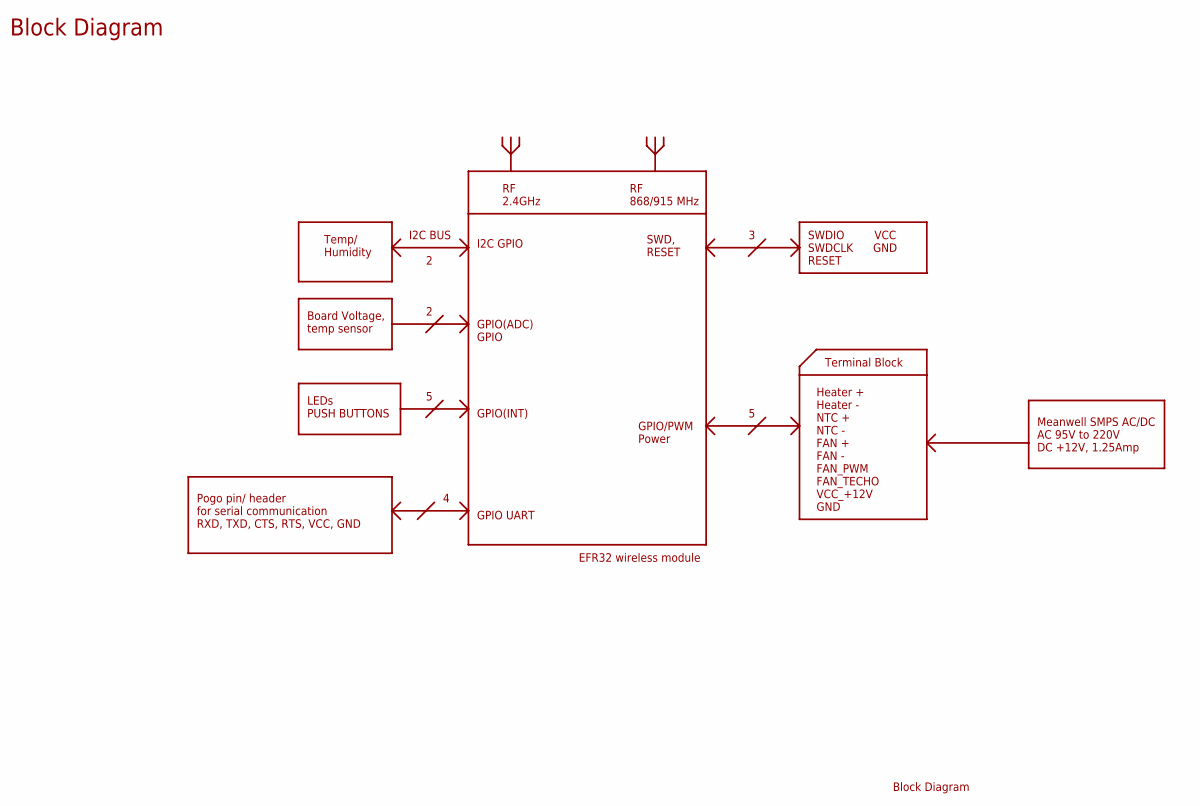
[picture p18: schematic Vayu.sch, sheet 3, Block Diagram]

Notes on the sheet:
Block Diagram
RF 2.4GHz
RF 868/915 MHz
SWD, RESET
SWDIO VCC SWDCLK GND RESET
Terminal Block
Heater + Heater - NTC + NTC - FAN + FAN - FAN_PWM FAN_TECHO VCC_+12V GND
Meanwell SMPS AC/DC AC 95V to 220V DC +12V, 1.25Amp
GPIO/PWM Power
GPIO UART
Pogo pin/ header for serial communication RXD, TXD, CTS, RTS, VCC, GND
I2C BUS
Temp/ Humidity
Board Voltage, temp sensor
LEDs PUSH BUTTONS
I2C GPIO
GPIO(ADC) GPIO
GPIO(INT)
EFR32 wireless module

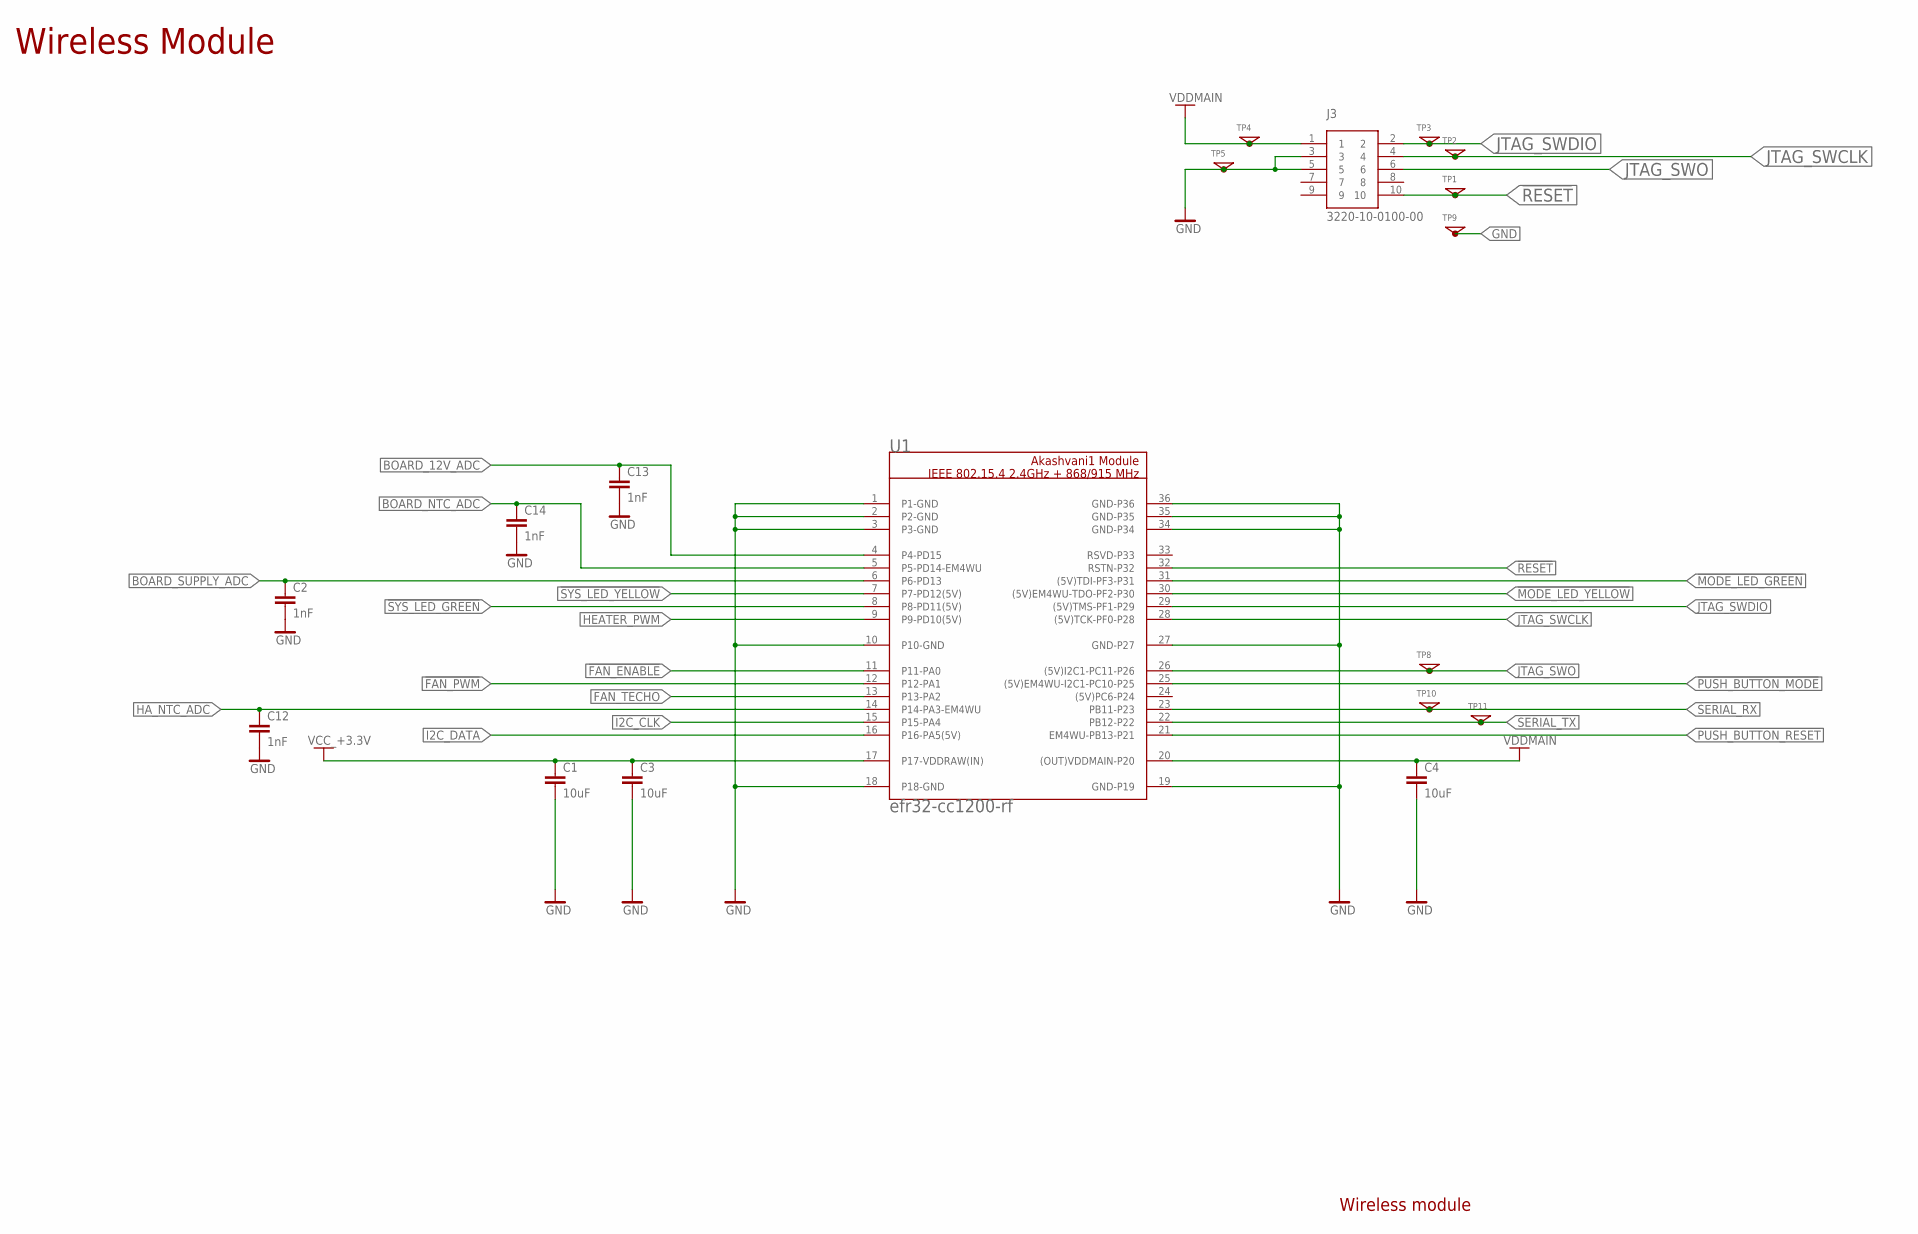
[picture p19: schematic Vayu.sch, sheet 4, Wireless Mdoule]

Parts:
C1, C3, C4: 10uF; C0603
C2, C12, C13, C14: 1nF; CAPC1005X55N
J3: 3220-10-0100-00; PIN2X5_1.27MM
TP1, TP2, TP3, TP4, TP5, TP8, TP9, TP10, TP11: TP_1.2
U1: efr32-cc1200-rf; AKASHVANI1

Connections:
!FAN_ENABLE: U1.11 (P11-PA0); also elsewhere on the board
!FAN_PWM: U1.12 (P12-PA1); also elsewhere on the board
!MODE_LED_GREEN: U1.31 ((5V)TDI-PF3-P31); also elsewhere on the board
!MODE_LED_YELLOW: U1.30 ((5V)EM4WU-TDO-PF2-P30); also elsewhere on the board
!PUSH_BUTTON_MODE: U1.25 ((5V)EM4WU-I2C1-PC10-P25); also elsewhere on the board
!PUSH_BUTTON_RESET: U1.21 (EM4WU-PB13-P21); also elsewhere on the board
!RESET: J3.10, TP1.1, U1.32 (RSTN-P32)
!SYS_LED_GREEN: U1.8 (P8-PD11(5V)); also elsewhere on the board
!SYS_LED_YELLOW: U1.7 (P7-PD12(5V)); also elsewhere on the board
BOARD_12V_ADC: C13.1, U1.4 (P4-PD15); also elsewhere on the board
BOARD_NTC_ADC: C14.1, U1.5 (P5-PD14-EM4WU); also elsewhere on the board
BOARD_SUPPLY_ADC: C2.1, U1.6 (P6-PD13); also elsewhere on the board
FAN_TECHO: U1.13 (P13-PA2); also elsewhere on the board
GND: C1.2, C2.2, C3.2, C4.2, C12.2, C13.2, C14.2, J3.3, J3.5, TP5.1, TP9.1, U1.1 (P1-GND), U1.2 (P2-GND), U1.3 (P3-GND), U1.10 (P10-GND), U1.18 (P18-GND), U1.19 (GND-P19), U1.27 (GND-P27), U1.34 (GND-P34), U1.35 (GND-P35), U1.36 (GND-P36); also elsewhere on the board
HA_NTC_ADC: C12.1, U1.14 (P14-PA3-EM4WU); also elsewhere on the board
HEATER_PWM: U1.9 (P9-PD10(5V)); also elsewhere on the board
I2C_CLK: U1.15 (P15-PA4); also elsewhere on the board
I2C_DATA: U1.16 (P16-PA5(5V)); also elsewhere on the board
JTAG_SWCLK: J3.4, TP2.1, U1.28 ((5V)TCK-PF0-P28)
JTAG_SWDIO: J3.2, TP3.1, U1.29 ((5V)TMS-PF1-P29)
JTAG_SWO: J3.6, TP8.1, U1.26 ((5V)I2C1-PC11-P26)
SERIAL_RX: TP10.1, U1.23 (PB11-P23)
SERIAL_TX: TP11.1, U1.22 (PB12-P22)
VCC_+3.3V: C1.1, C3.1, U1.17 (P17-VDDRAW(IN)); also elsewhere on the board
VDDMAIN: C4.1, J3.1, TP4.1, U1.20 ((OUT)VDDMAIN-P20); also elsewhere on the board

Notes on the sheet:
Wireless module
Wireless Module

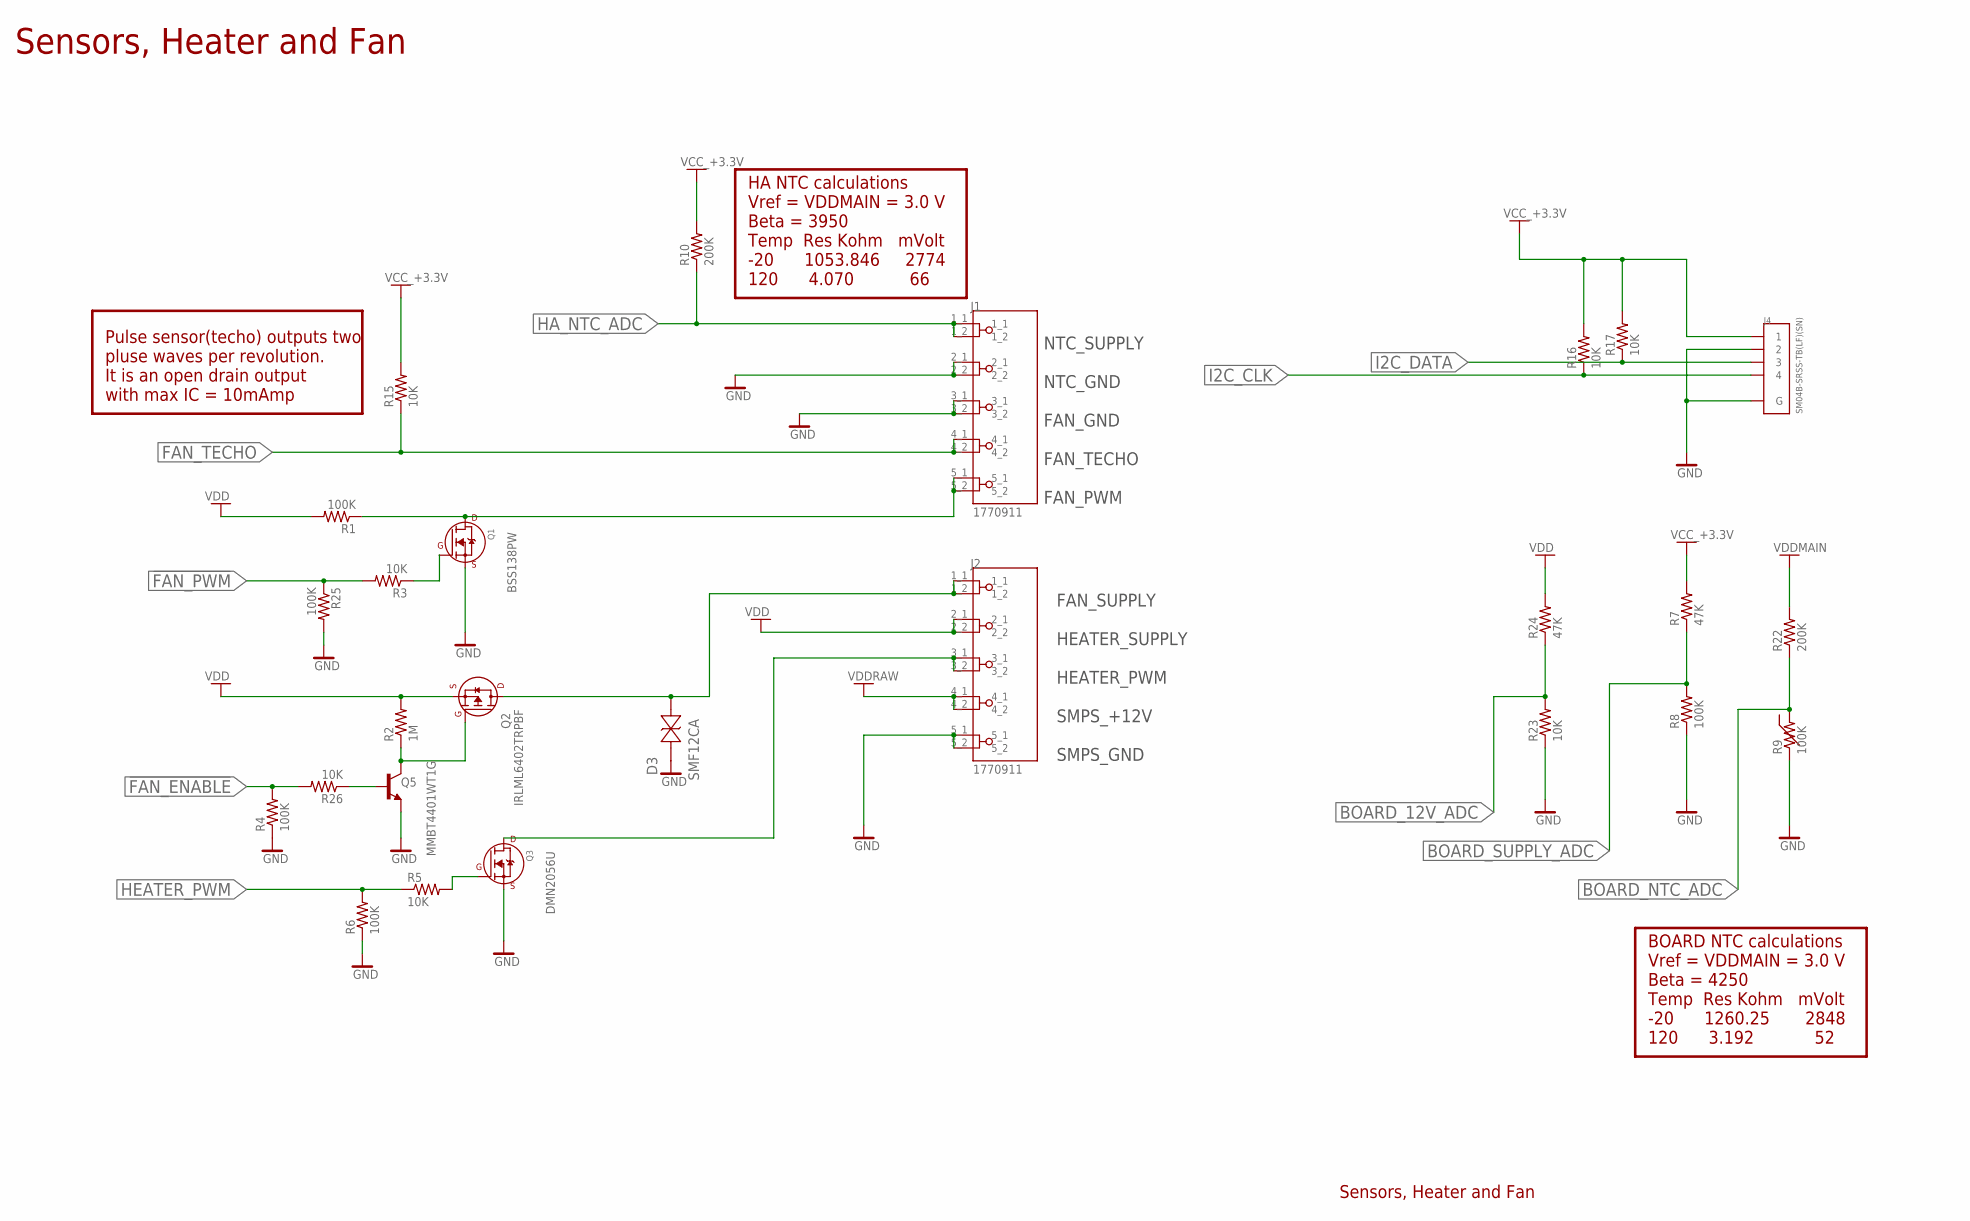
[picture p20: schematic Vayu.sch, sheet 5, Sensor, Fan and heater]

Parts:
D3: SMF12CA; SOD-123F-BI
J1, J2: 1770911; PHOENIX_1770911
J4: SM04B-SRSS-TB(LF)(SN); JST_SM04B-SRSS-TB(LF)(SN)
Q1: BSS138PW; SC-70_SOT323
Q2: IRLML6402TRPBF; SOT23-3
Q3: DMN2056U; SOT23-3
Q5: MMBT4401WT1G; SOT323-BEC
R1, R4, R6, R8, R9, R25: 100K; R0402
R2: 1M; R0402
R3, R5, R15, R16, R17, R23, R26: 10K; R0402
R7, R24: 47K; R0402
R10, R22: 200K; R0402

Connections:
!FAN_ENABLE: R4.2, R26.2; also elsewhere on the board
!FAN_PWM: R3.2, R25.1; also elsewhere on the board
BOARD_12V_ADC: R23.2, R24.1; also elsewhere on the board
BOARD_NTC_ADC: R9.2, R22.1; also elsewhere on the board
BOARD_SUPPLY_ADC: R7.1, R8.2; also elsewhere on the board
FAN_SPEED: J1.5_1, J1.5_2, Q1.3 (D), R1.1
FAN_SUPPLY: D3.1 (11), J2.1_1, J2.1_2, Q2.D
FAN_TECHO: J1.4_1, J1.4_2, R15.1; also elsewhere on the board
GND: D3.2 (12), J1.2_1, J1.2_2, J1.3_1, J1.3_2, J2.5_1, J2.5_2, J4.2, J4.S1 (G), J4.S2 (G), Q1.2 (S), Q3.S, Q5.E, R4.1, R6.1, R8.1, R9.1, R23.1, R25.2; also elsewhere on the board
HA_NTC_ADC: J1.1_1, J1.1_2, R10.1; also elsewhere on the board
HEATER: J2.3_1, J2.3_2, Q3.D
HEATER_PWM: R5.1, R6.2; also elsewhere on the board
I2C_CLK: J4.4, R16.1; also elsewhere on the board
I2C_DATA: J4.3, R17.1; also elsewhere on the board
unnamed: Q1.1 (G), R3.1
unnamed: Q3.G, R5.2
unnamed: Q5.B, R26.1
PMOSFET_EN: Q2.G, Q5.C, R2.1
VCC_+3.3V: J4.1, R7.2, R10.2, R15.2, R16.2, R17.2; also elsewhere on the board
VDD: J2.2_1, J2.2_2, Q2.S, R1.2, R2.2, R24.2; also elsewhere on the board
VDDMAIN: R22.2; also elsewhere on the board
VDDRAW: J2.4_1, J2.4_2; also elsewhere on the board

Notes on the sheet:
Sensors, Heater and Fan
Pulse sensor(techo) outputs two pluse waves per revolution. It is an open drain output with max IC = 10mAmp
NTC_SUPPLY NTC_GND FAN_GND FAN_TECHO FAN_PWM
FAN_SUPPLY HEATER_SUPPLY HEATER_PWM SMPS_+12V SMPS_GND
HA NTC calculations Vref = VDDMAIN = 3.0 V Beta = 3950 Temp Res Kohm mVolt -20 1053.846 2774 120 4.070 66
BOARD NTC calculations Vref = VDDMAIN = 3.0 V Beta = 4250 Temp Res Kohm mVolt -20 1260.25 2848 120 3.192 52

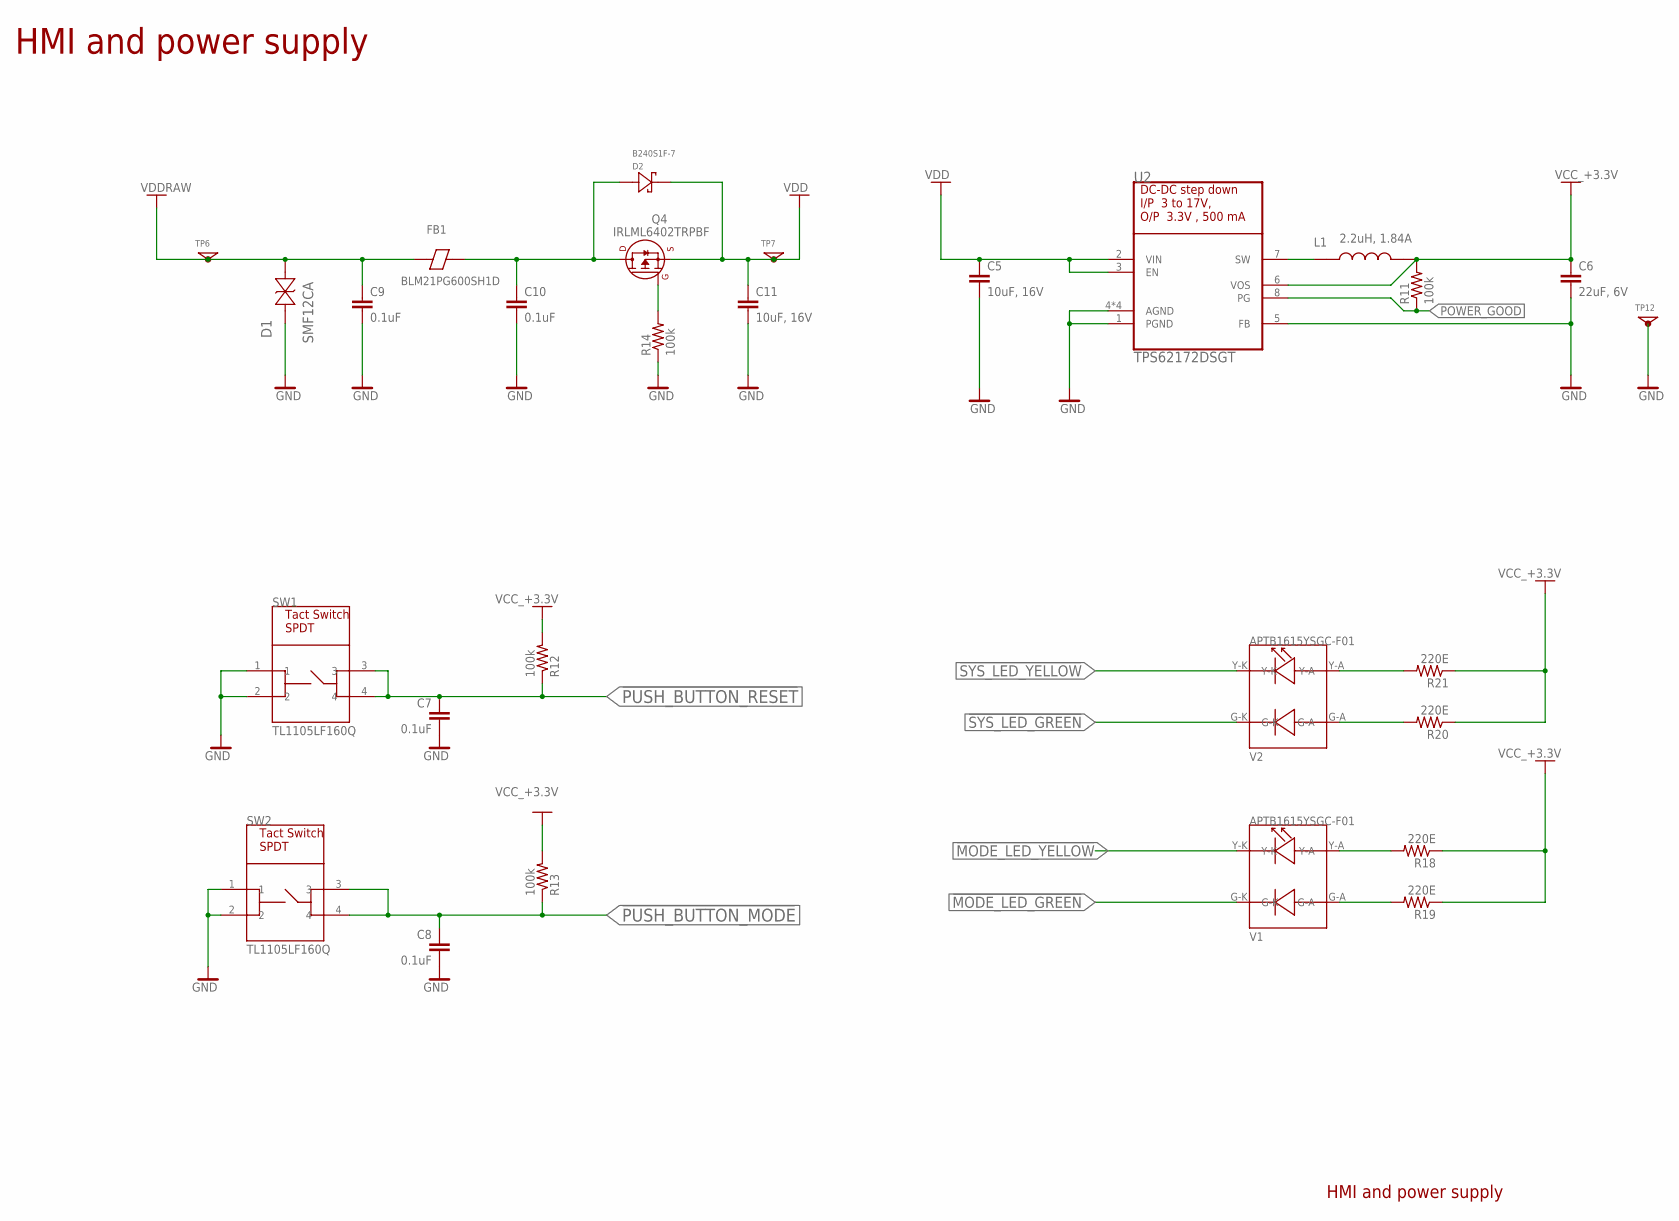
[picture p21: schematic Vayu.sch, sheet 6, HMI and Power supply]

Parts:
C5, C11: 10uF, 16V; C0805
C6: 22uF, 6V; C0603
C7, C8, C9, C10: 0.1uF; CAPC1005X55N
D1: SMF12CA; SOD-123F-BI
D2: B240S1F-7; SOD-123F
FB1: BLM21PG600SH1D; BEADC2012X105N
L1: 2.2uH, 1.84A; IND_VLS201612HBX-2R2M-1
Q4: IRLML6402TRPBF; SOT23-3
R11, R12, R13, R14: 100k; R0402
R18, R19, R20, R21: 220E; R0402
SW1, SW2: TL1105LF160Q; TACT_TH_6X6X17MM
TP6, TP7, TP12: TP_1.2
U2: TPS62172DSGT; SON50P200X200X80-9N
V1, V2: APTB1615YSGC-F01; LED-0606

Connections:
!MODE_LED_GREEN: V1.G-K; also elsewhere on the board
!MODE_LED_YELLOW: V1.Y-K; also elsewhere on the board
!PUSH_BUTTON_MODE: C8.1, R13.1, SW2.3, SW2.4; also elsewhere on the board
!PUSH_BUTTON_RESET: C7.1, R12.1, SW1.3, SW1.4; also elsewhere on the board
!SYS_LED_GREEN: V2.G-K; also elsewhere on the board
!SYS_LED_YELLOW: V2.Y-K; also elsewhere on the board
GND: C5.2, C6.2, C7.2, C8.2, C9.2, C10.2, C11.2, D1.2 (12), R14.1, SW1.1, SW1.2, SW2.1, SW2.2, TP12.1, U2.1 (PGND), U2.4 (AGND), U2.5 (FB), U2.9 (AGND), U2.9_1 (AGND), U2.9_2 (AGND); also elsewhere on the board
unnamed: L1.1, U2.7 (SW)
unnamed: C10.1, D2.A, FB1.2, Q4.D
unnamed: Q4.G, R14.2
unnamed: R21.2, V2.Y-A
unnamed: R20.2, V2.G-A
unnamed: R18.2, V1.Y-A
unnamed: R19.2, V1.G-A
POWER_GOOD: R11.1, U2.8 (PG)
VCC_+3.3V: C6.1, L1.2, R11.2, R12.2, R13.2, R18.1, R19.1, R20.1, R21.1, U2.6 (VOS); also elsewhere on the board
VDD: C5.1, C11.1, D2.K, Q4.S, TP7.1, U2.2 (VIN), U2.3 (EN); also elsewhere on the board
VDDRAW: C9.1, D1.1 (11), FB1.1, TP6.1; also elsewhere on the board

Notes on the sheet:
HMI and power supply

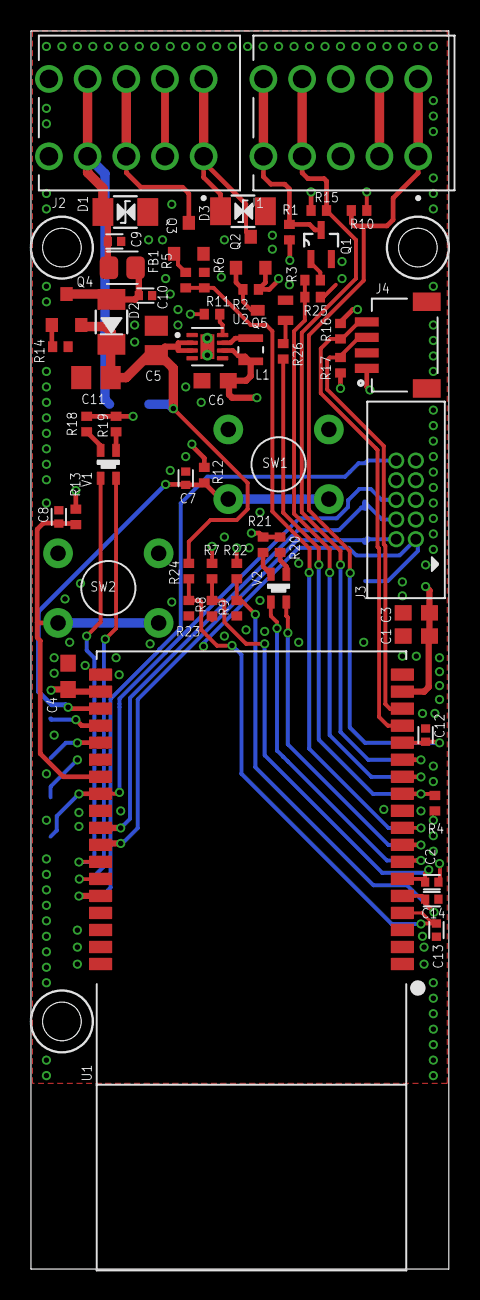
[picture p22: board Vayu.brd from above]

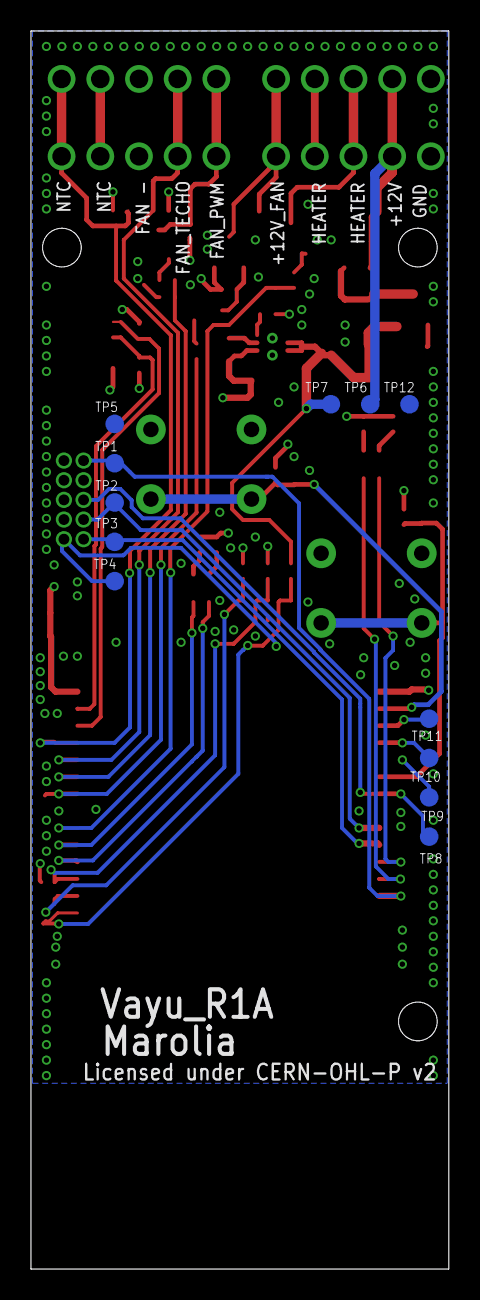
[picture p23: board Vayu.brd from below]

Board: 4 copper layers, 27.0 x 80.0 mm, 72 parts (12 on the bottom side), 42 nets.

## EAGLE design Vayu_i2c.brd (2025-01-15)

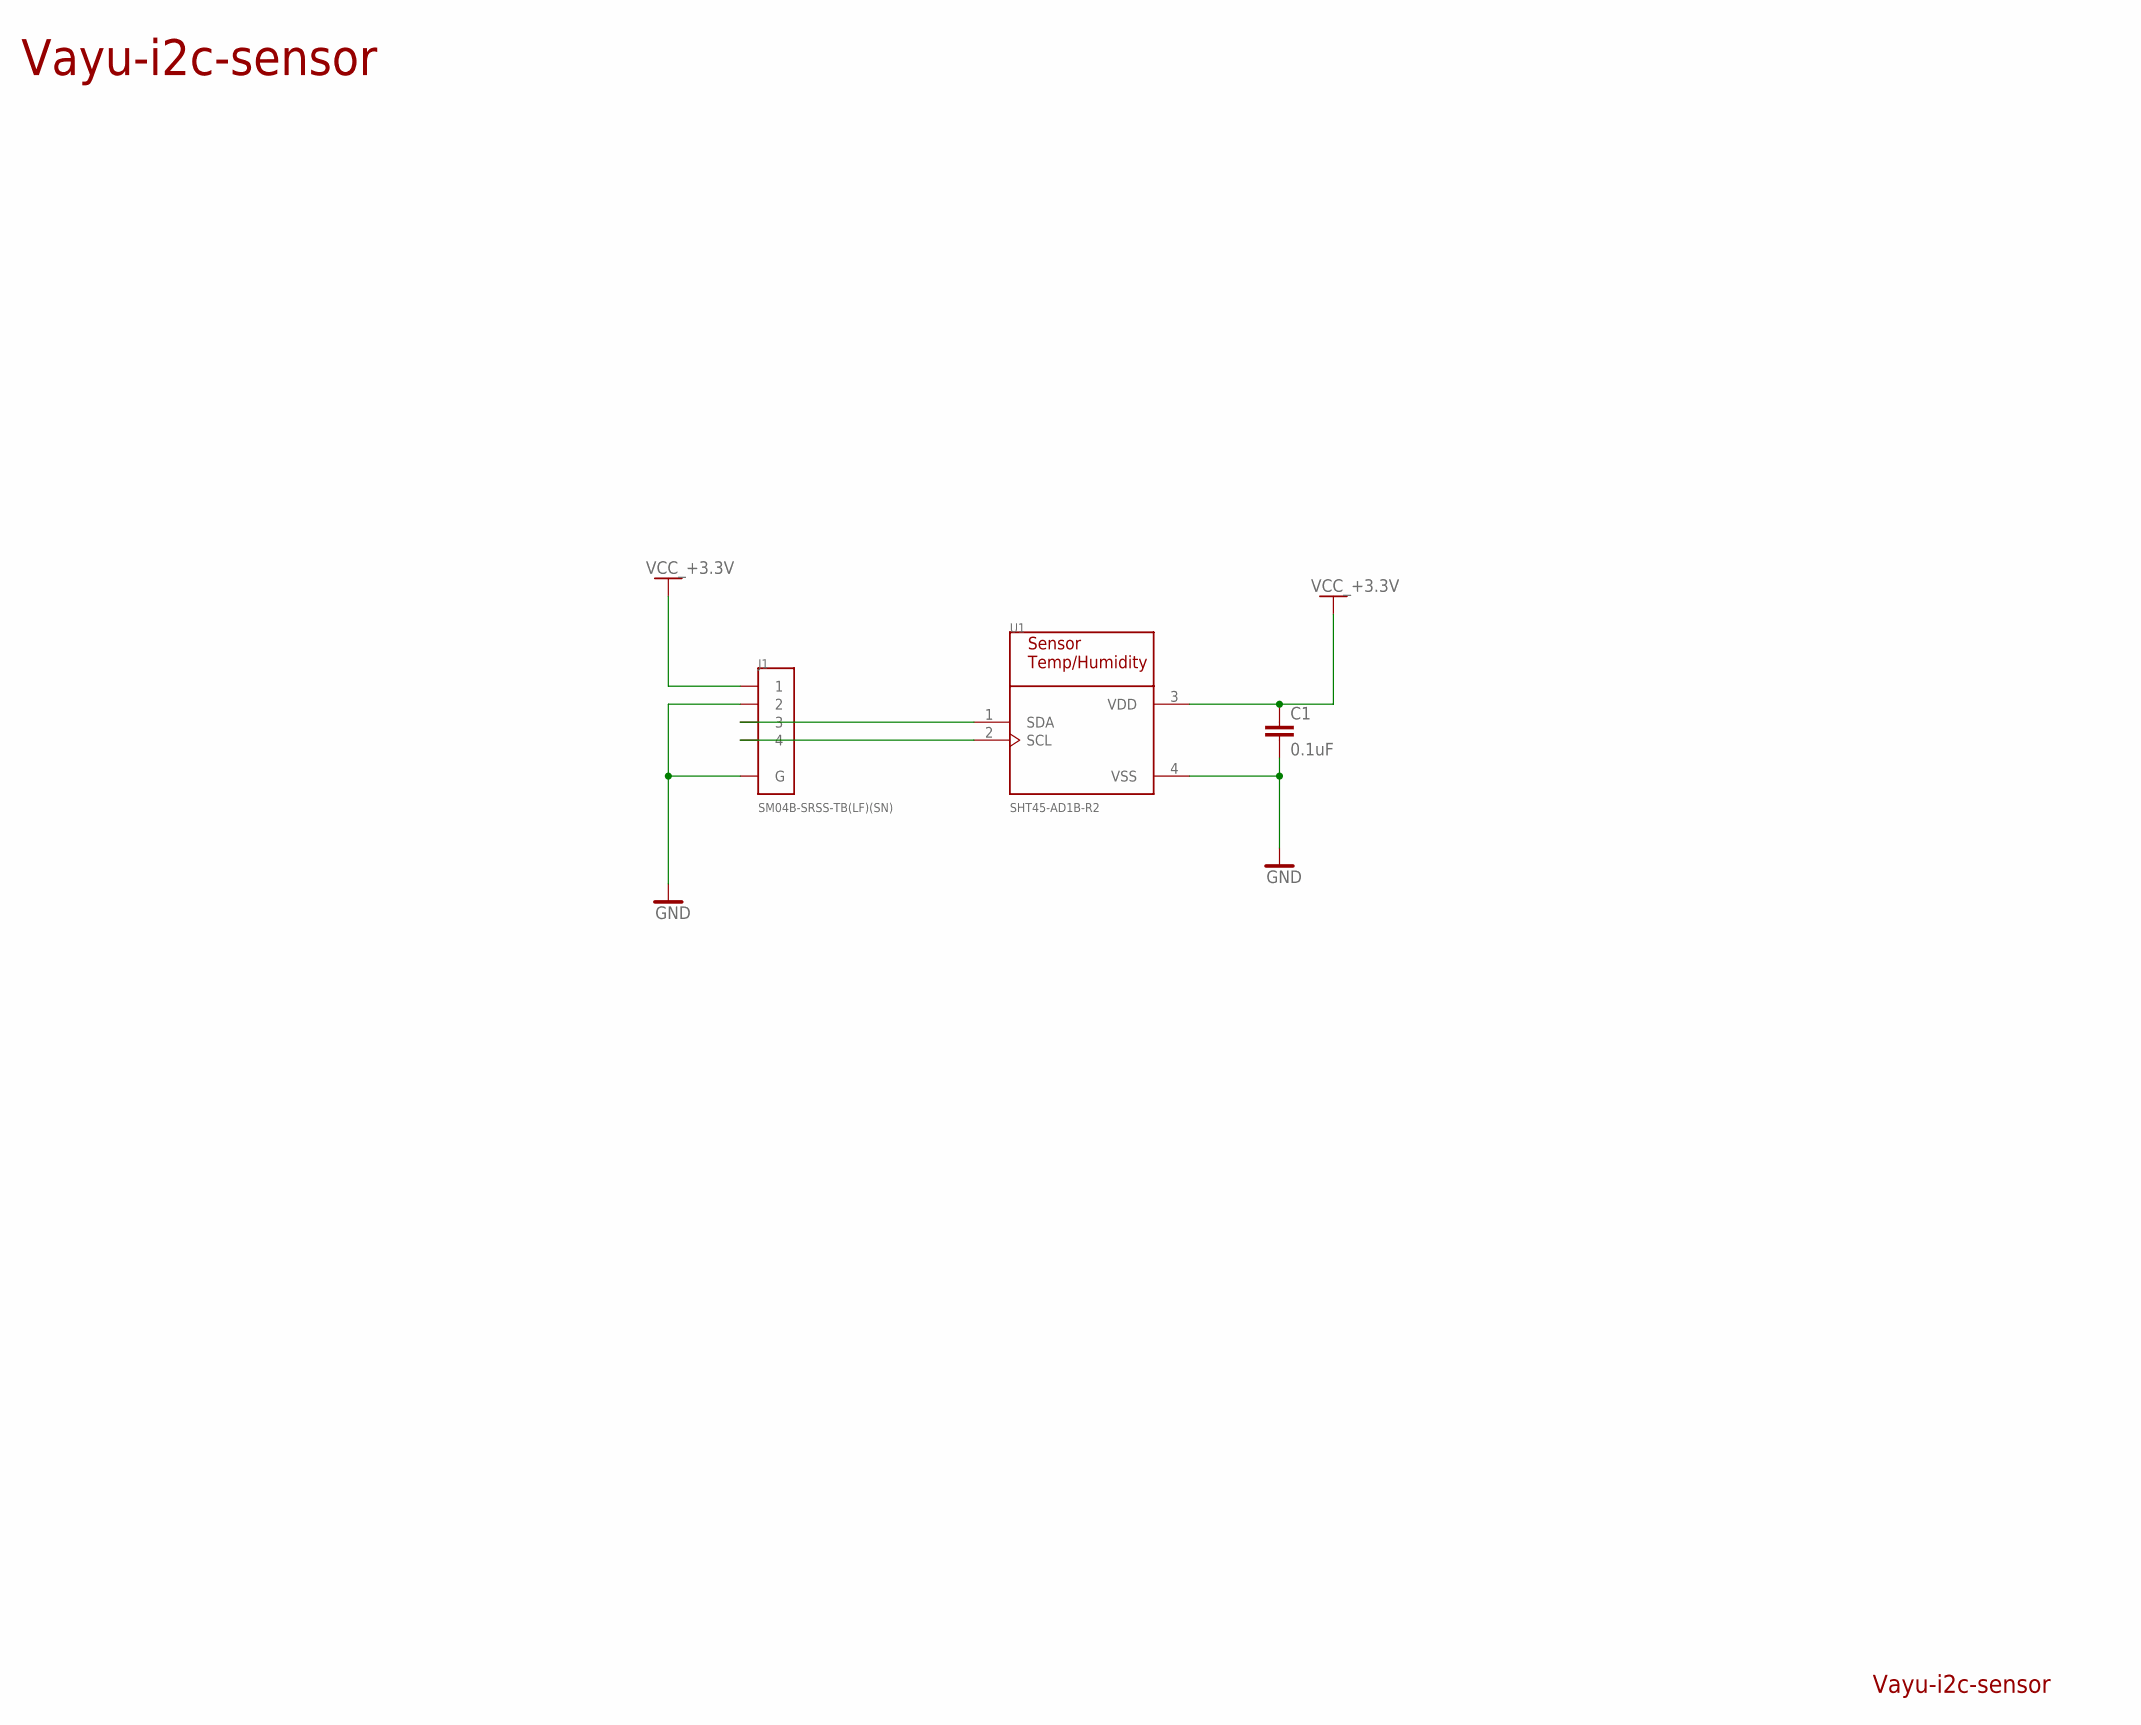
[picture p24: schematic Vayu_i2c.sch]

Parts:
C1: 0.1uF; C0402
J1: SM04B-SRSS-TB(LF)(SN); JST_SM04B-SRSS-TB(LF)(SN)
U1: SHT45-AD1B-R2; XDCR_SHT45-AD1B-R2

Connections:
GND: C1.2, J1.2, J1.S1 (G), J1.S2 (G), U1.4 (VSS)
unnamed: J1.3, U1.1 (SDA)
unnamed: J1.4, U1.2 (SCL)
VCC_+3.3V: C1.1, J1.1, U1.3 (VDD)

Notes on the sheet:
Vayu-i2c-sensor

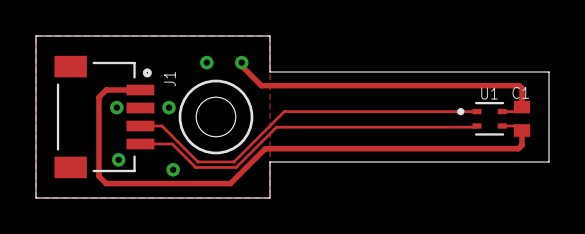
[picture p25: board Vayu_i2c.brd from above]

Board: 2 copper layers, 28.5 x 9.0 mm, 3 parts (0 on the bottom side), 4 nets.

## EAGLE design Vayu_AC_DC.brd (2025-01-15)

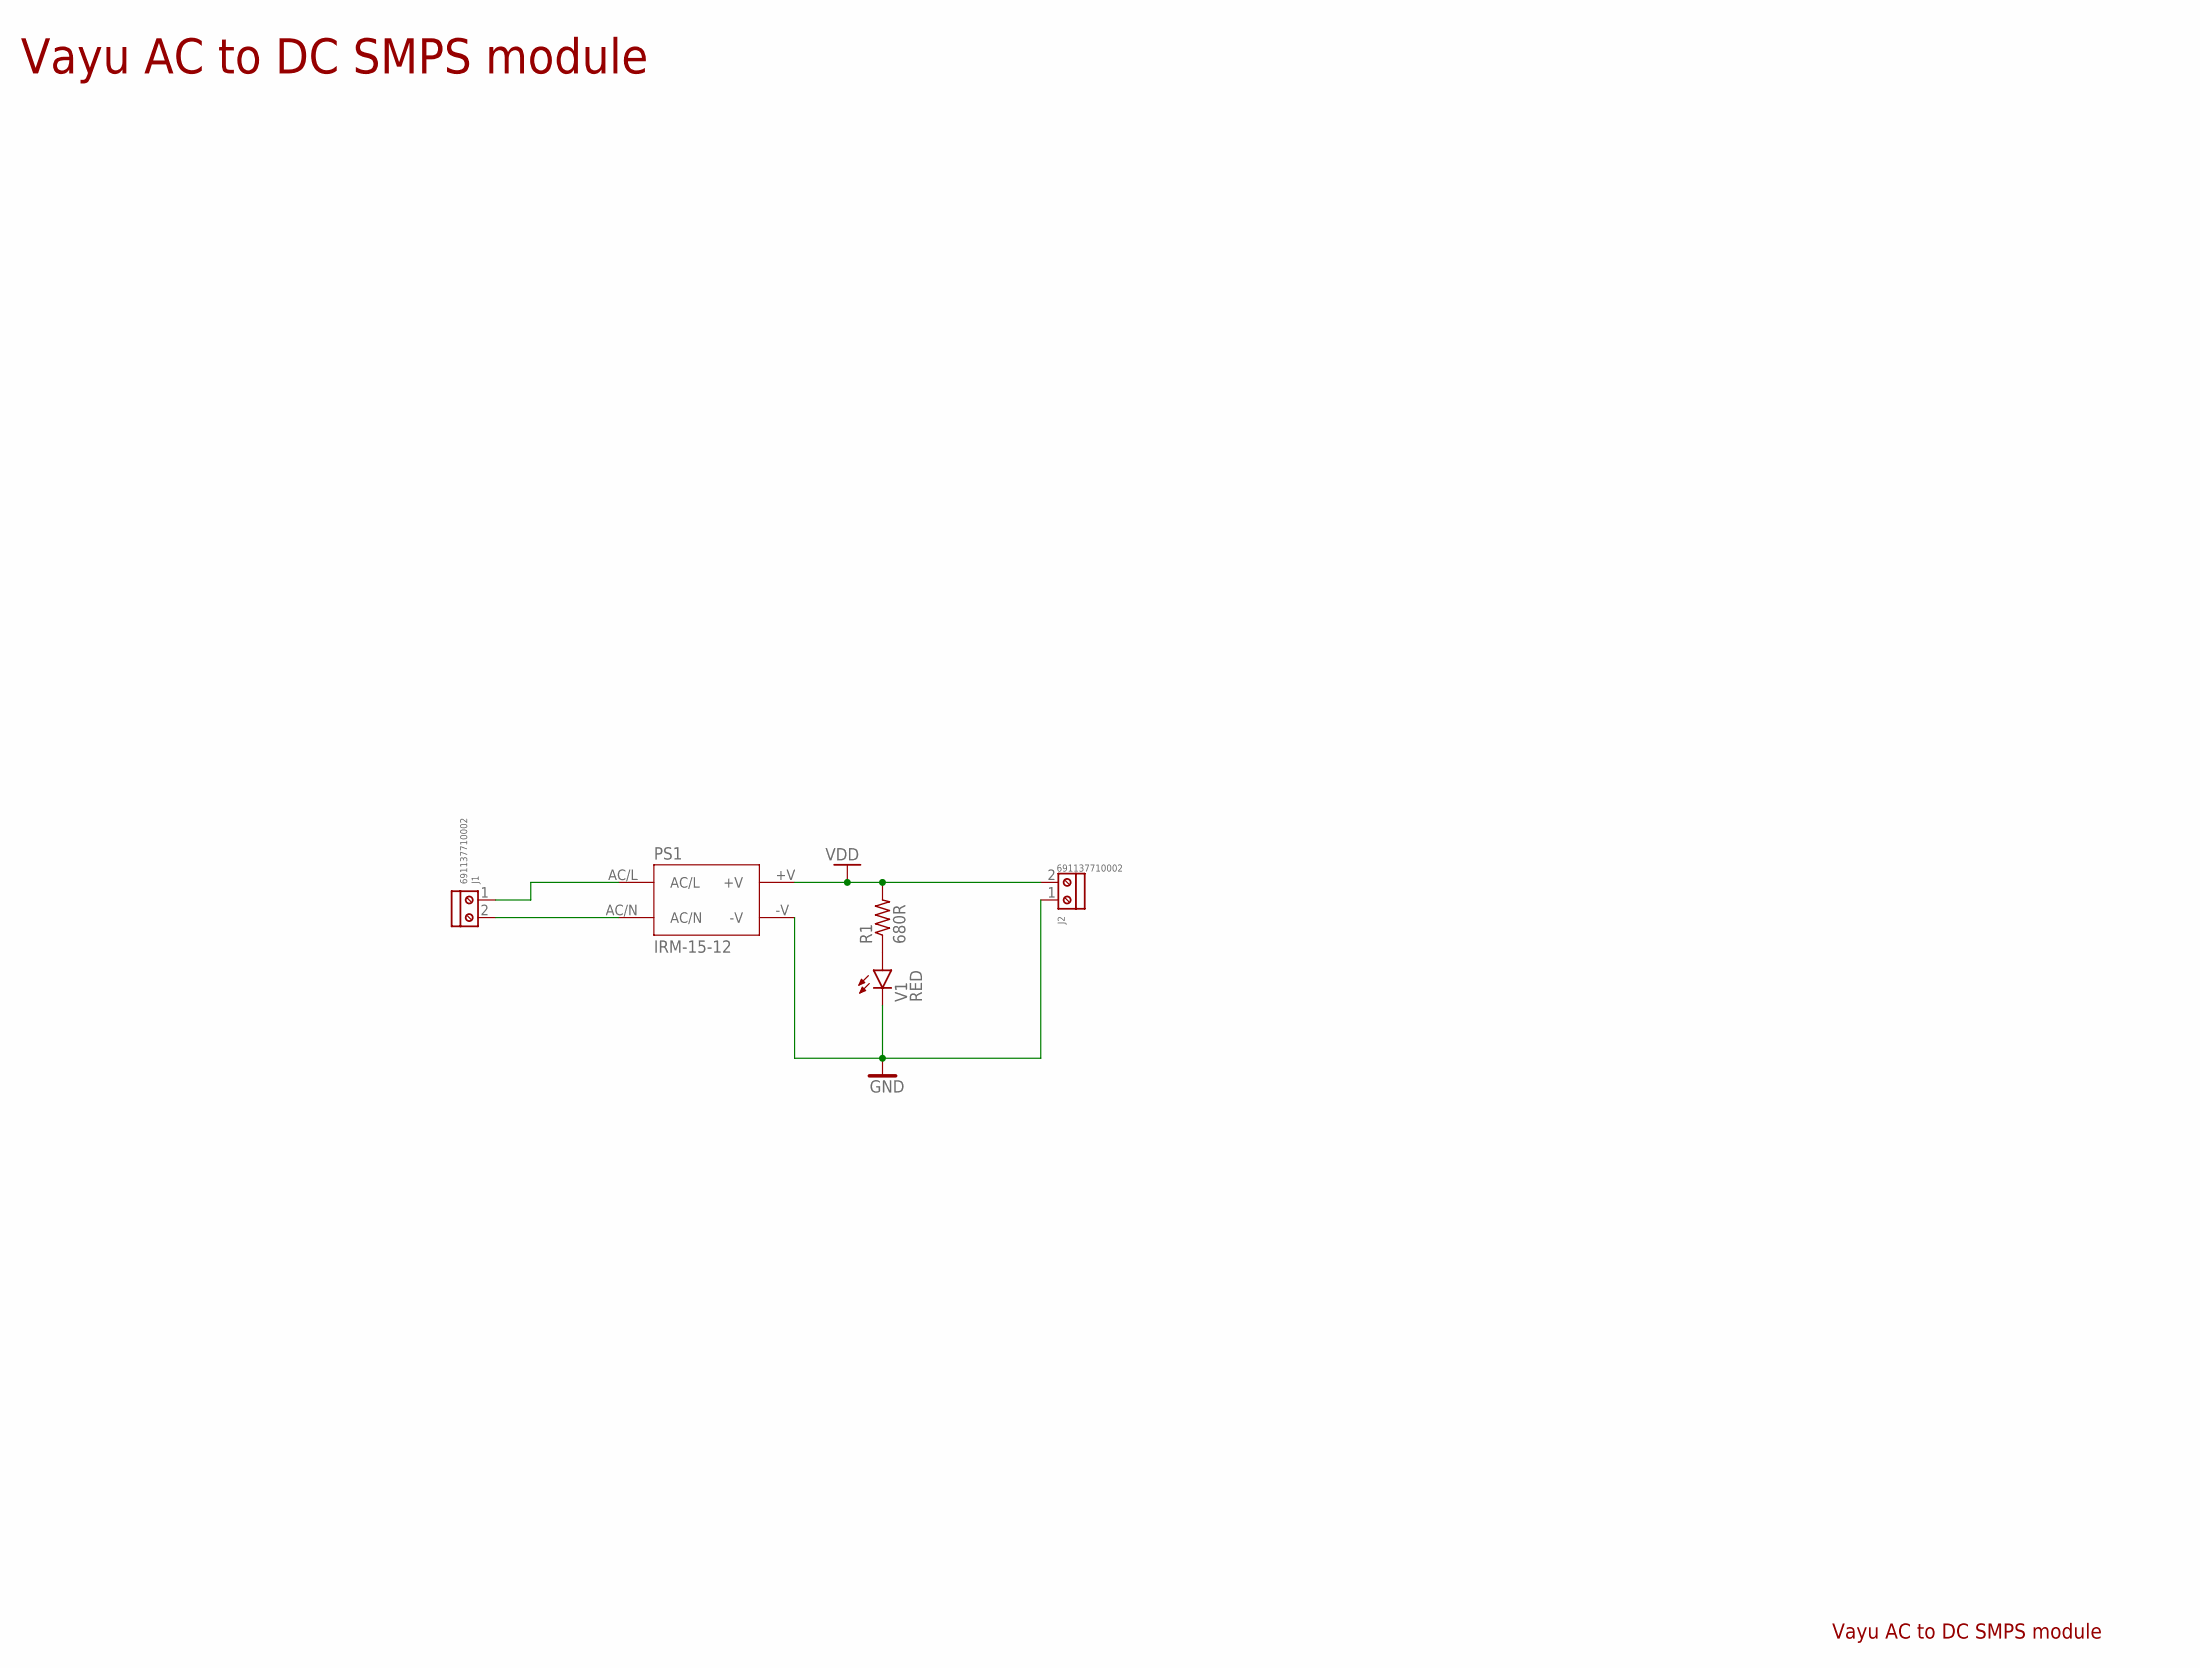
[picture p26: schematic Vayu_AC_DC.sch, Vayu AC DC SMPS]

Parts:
J1, J2: 691137710002
PS1: IRM-15-12; CONV_IRM-15-12
R1: 680R; R0402
V1: RED; CHIP-LED0603

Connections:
AC/L: J1.1, PS1.AC/L
AC/N: J1.2, PS1.AC/N
GND: J2.1, PS1.-V, V1.C
unnamed: R1.1, V1.A
VDD: J2.2, PS1.+V, R1.2

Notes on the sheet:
Vayu AC to DC SMPS module

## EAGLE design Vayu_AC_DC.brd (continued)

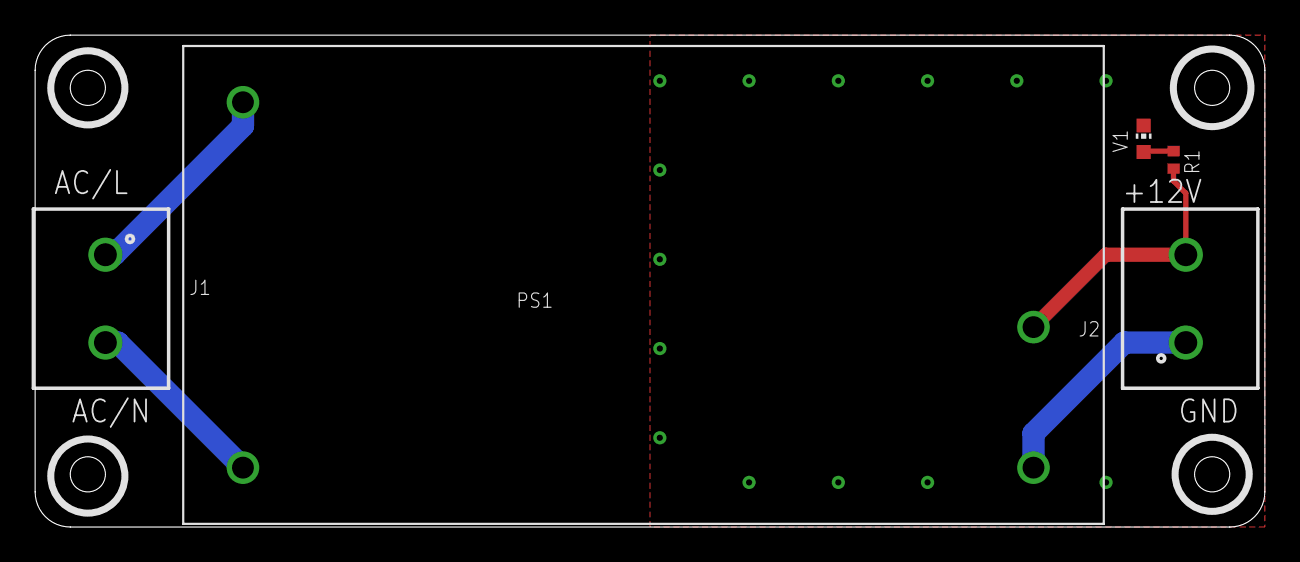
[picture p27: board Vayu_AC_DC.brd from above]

Board: 2 copper layers, 70.0 x 28.0 mm, 5 parts (0 on the bottom side), 5 nets.

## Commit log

2025-01-15 Added ignore and new raw files after complete data loss!
    [Vayu.brd, Vayu.sch, Vayu_AC_DC.brd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]
2025-01-15 Added gerber files updated schematic files
    [copper_bottom.gbr, copper_bottom_l4.gbr, copper_inner_l2.gbr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]
2025-01-15 Added dru, updated board thermal mask, added Vayu bom file
    [Vayu.brd, bom-Vayu-R1A.xlsx]
2025-01-16 Added BOM files for sensor, AC-DC and top level
    [bom-Vayu-R1A.xlsx, bom-Vayu-prod-rev-p01.xlsx, bom-Vayu_AC_DC-R1A.xlsx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]
2025-01-16 Added magnet
    [bom-Vayu-prod-rev-p01.xlsx]
2025-01-17 Added heater,tape and NTC
    [bom-Vayu-prod-rev-p01.xlsx]
2025-03-12 removed sch bugs and WIP in brd
    [Vayu.brd, Vayu.sch]
2025-03-14 bug fix, updated MOSFET driver and other MOSFETS, added SWO support
    [Vayu.brd, Vayu.sch, bom-Vayu-R1A.xlsx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]

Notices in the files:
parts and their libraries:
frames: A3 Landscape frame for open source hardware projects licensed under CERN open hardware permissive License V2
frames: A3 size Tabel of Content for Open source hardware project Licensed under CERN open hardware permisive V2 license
